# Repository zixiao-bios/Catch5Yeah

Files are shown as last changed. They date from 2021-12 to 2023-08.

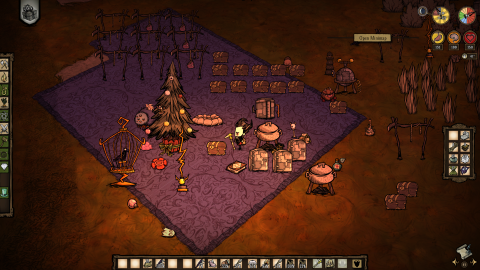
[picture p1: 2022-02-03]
ArtDesign/imgs/img_DST.png

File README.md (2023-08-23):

# Catch5Yeah

 A DIY claw machine as our 5th anniversary gift.

Assembly and operation video on bilibili: https://www.bilibili.com/video/BV1fP411p73M/

vlcsnap-2023-08-23-16h21m46s423

封面



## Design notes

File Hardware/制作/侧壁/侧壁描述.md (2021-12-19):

### 总览

+ 高度：650mm
+ 外径：400mm
+ 壁厚：5mm

共有 4 个特征：

+ 4 个顶部 L 形开槽
+ 1 个侧面圆角矩形开孔
+ 1 正面底部个方形开槽
+ 1 个背面底部胶囊形开孔

立体图如下：




俯视图相对位置：



下面一一说明每个特征的细节，下文中长度单位均为 mm，使用角度制。

### 4 个顶部 L 形开槽



+ 右图三个蓝色的平面都是**径向**的，不互相平行

### 1 个侧面圆角矩形开孔



+ 右图两个蓝色的平面是**平行**的

### 1 正面底部个方形开槽



+ 上图两个蓝色的平面是**径向**的，不平行

### 1 个背面底部胶囊形开孔



+ 上图两个蓝色平面是**平行**的

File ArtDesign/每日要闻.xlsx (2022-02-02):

配图 | 文字
饥荒小家 | 考古重大发现：x千万年历史洞穴发现史前壁画、火堆、烧焦的骨头等，将人类用火的历史提前，壁画内容改变人类对史前认知。网友指出壁画内容为知名生存游戏“饥荒”，游戏工作室科雷经过调查后发表声明称，该壁画系饥荒团队外出团建时，美工部门员工一时兴起所作，而火堆等痕迹系烧烤后的残留物。消息公布后国际社会对其破坏史前洞穴的行为一片谴责，受此负面消息影响，腾讯公司股价下跌超过10%，为今年最大单日跌幅。
坎巴拉合影 | NASA最新太空望远镜詹姆斯韦伯完成初期调试工作，向比邻星拍摄了第一张照片。竟然拍到了两个外星个体乘坐露天飞船远航的景象。照片一经爆出即掀起巨大舆论，主流舆论认为此为流浪太空的两个善良外星人，并在众筹网站发布名为“小绿人也是人，他们需要一个家！”的众筹项目。另有网友指出，该形象与知名航天沙盒游戏“Kerbal Space Programme”中十分相似，并据此推断该工作室早已与该文明建立秘密联系，并引导其攻占地球。但Xxx工作室公关部坚称该形象源自CEO儿子三岁时的美术作业。
美女亲嘴 | 新晋网红“露露奶黄包”，人民日报评论员文章："审丑"风气不可有

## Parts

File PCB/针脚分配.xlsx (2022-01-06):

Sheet: ESP32
GPIO | Intput | Output | Notes | 分配 | Function
0 | pulled up | OK | outputs PWM signal at boot Strapping pin | 74HC595D_SCK
1 | TX Pin | OK | debug output at boot | RGB2
2 | OK | OK | connected to on-board LED strapping pin | 74HC595D_RCK
3 | OK | RX Pin | HIGH at boot | K2
4 | OK | OK |  | TFT_MISO
5 | OK | OK | outputs PWM signal at boot strapping pin | TFT_MOSI
6 | NO | NO | 连接到集成 SPI Flash
7 | NO | NO | 连接到集成 SPI Flash
8 | NO | NO | 连接到集成 SPI Flash
9 | NO | NO | 连接到集成 SPI Flash
10 | NO | NO | 连接到集成 SPI Flash
11 | NO | NO | 连接到集成 SPI Flash
12 | OK | OK | boot fail if pulled high strapping pin | I2S_BLCK
13 | OK | OK |  | I2S_DIN
14 | OK | OK | outputs PWM signal at boot | I2S_LRC
15 | OK | OK | outputs PWM signal at boot strapping pin | 74HC595D_SI
16 | OK | OK |  | RTC_SCL
17 | OK | OK |  | TFT_SCLK
18 | OK | OK |  | TFT_DC
19 | OK | OK |  | RTC_SDA
21 | OK | OK |  | TFT_CS
22 | OK | OK |  | TOUCH_CS
23 | OK | OK |  | RGB1
25 | OK | OK |  | RGB3
26 | OK | OK |  | K1
27 | OK | OK |  | RGB4
32 | OK | OK |  | K3
33 | OK | OK |  | K4
34 | OK | NO | input only | S3
35 | OK | NO | input only | B1
36 | OK | NO | input only | S1
39 | OK | NO | input only | S2

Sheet: 74HC595D
Pin | 分配
Q0/QA
Q1/QB | MOTOR1
Q2/QC | MOTOR1
Q3/QD | MOTOR2
Q4/QE | MOTOR2
Q5/QF | MOTOR3
Q6/QG | MAG
Q7/QH | TFT_LED

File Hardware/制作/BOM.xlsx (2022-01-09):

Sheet: 紧固件
类别 | 型号 | 用途 | 数量 | 备注
弹簧垫圈 | M3 | 操纵台-屏幕-底板 | 4
垫圈 | M3*5*0.5 | 操纵台-屏幕-底板 | 4
弹簧垫圈 | M5 | 操纵台-摇杆-底板 | 4
平头螺丝 | M5*12 | 操纵台-摇杆-底板 | 4
平头螺丝 | M3*10 | 操纵台-屏幕-底板 | 4
防松螺母 | M5 | 操纵台-侧壁 | 2
平头螺丝 | M5*12 | 操纵台-侧壁 | 2
平头螺丝 | M5*12 | 操纵台-底板 | 4
弹簧垫圈 | M5 | 操纵台-底板 | 4
防松螺母 | M5 | 底板-侧壁 | 5
平头螺丝 | M5*12 | 底板-侧壁 | 5
薄螺母 | M4 | 底板-电机 | 4
弹簧垫圈 | M4 | 底板-电机 | 4
平头螺丝 | M4*10 | 底板-电机 | 4
防松螺母 | M5 | 顶盖-L锁 | 8
平头螺丝 | M5*35 | 顶盖-L锁 | 8
防松螺母 | M5 | 顶盖-皮带从动轮 | 2
平头螺丝 | M5*12 | 顶盖-皮带从动轮 | 2
防松螺母 | M5 | 顶盖-皮带主动轮 | 2
平头螺丝 | M5*18 | 顶盖-皮带主动轮 | 2
防松螺母 | M5 | 顶盖-顶盖密码锁 | 2
平头螺丝 | M5*12 | 顶盖-顶盖密码锁 | 2
防松螺母 | M5 | 侧壁-侧壁密码锁 | 2
平头螺丝 | M5*12 | 侧壁-侧壁密码锁 | 2
防松螺母 | M3 | 顶盖-滑块止动块 | 2
平头螺丝 | M3*20 | 顶盖-滑块止动块 | 2
平头螺丝 | M3*6 | 底板-开关电源 | 4
防松螺母 | M2.5 | 吊轮架-皮带扣 | 4
弹簧垫圈 | M2 | N20减速电机-皮带主动轮架 | 2
平头螺丝 | M2*8 | 顶盖密码锁-弹簧触点 | 1
平头螺丝 | M2*16 | 顶盖密码锁-弹簧触点 | 1
防松螺母 | M2 | 顶盖密码锁-弹簧触点 | 2
防松螺母 | M3 | 顶盖-灯条固定架 | 2
平头螺丝 | M3*10 | 顶盖-灯条固定架 | 2
防松螺母 | M3 | 红外接近开关 | 3
平头螺丝 | M3*10 | 红外接近开关 | 2
平头螺丝 | M3*10 | 红外接近开关 | 1
防松螺母 | M2.5 | 电磁铁架-导线扣 | 2
平头螺丝 | M2.5*8 | 电磁铁架-导线扣 | 2
平头螺丝 | M2.5*12 | 吊轮架-皮带扣 | 4
平头螺丝 | M4*10 | 吊轮架-滑块 | 4
弹簧垫圈 | M4 | 吊轮架-滑块 | 4
防松螺母 | M3 | 侧壁-出球口平台 | 4
平头螺丝 | M3*10 | 侧壁-出球口平台 | 4
热熔螺母 | M5*5*7 | 底板M5螺丝柱 | 8
热熔螺母 | M3*5*5 | 底板M3螺丝柱 | 4
热熔螺母 | M4*4*6 | 顶盖-滑轨 | 6
内六角螺丝 | M4*14 | 顶盖-滑轨 | 6
平头螺丝 | M3*10 | 转盘-传动法兰 | 4
防松螺母 | M3 | 转盘-传动法兰 | 4
平头螺丝 | M3*10 | 挡板-转盘 | 12
防松螺母 | M3 | 挡板-转盘 | 12
防松螺母 | M2 | RGB灯条卡槽-侧壁 | 16
平头螺丝 | M2*10 | RGB灯条卡槽-侧壁 | 16
平头螺丝 | M2*8 | 侧壁密码锁-弹簧触点 | 2
防松螺母 | M2 | 顶盖密码锁-弹簧触点 | 2
垫圈 | M4*7*1 | 吊轮架-滑块 | 4
平头螺丝 | M3*20 | 侧壁-AC电源插座 | 2
防松螺母 | M3 | 侧壁-AC电源插座 | 2
防松螺母 | M3 | 底板-PCB | 4
平头螺丝 | M3*10 | 底板-PCB | 4
垫圈 | M3*5*0.5 | 底板-PCB | 8
弹簧垫圈 | M3 | 底板-PCB | 4
平头螺丝 | M6*16 | 顶盖-提手 | 2
弹簧垫圈 | M6 | 顶盖-提手 | 2
垫圈 | M6*20*1 | 顶盖-提手 | 2

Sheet: 铁盒
名称 | 形状 | 内容 | 尺寸/mm | 数量
小猪佩奇集趣球 | 球形 | 奶片 | 70 | 12
0号球 | 球形 | 纪念 | 70 | 1
小方盒 | 方形 | 首饰 | 75*75*65
大方盒 | 方形 |  | 94*94*90
扁圆盒 | 包子 | 口红 | 90*90*65

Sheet: Sheet1
皮带扣 | 螺母位过大
线轮 | 凹槽过浅
吊轮架 | 降低皮带扣位置，以防止皮带空转
操作台 | 边缘突出底盘侧壁，中部低于侧壁开槽
RGB灯条卡槽 | 螺母位过大
L锁 | 突出部分位置过高
顶盖密码锁 | 去除弹簧触点支架
侧壁密码锁 | 密码锁开孔过小；去除弹簧触点支架

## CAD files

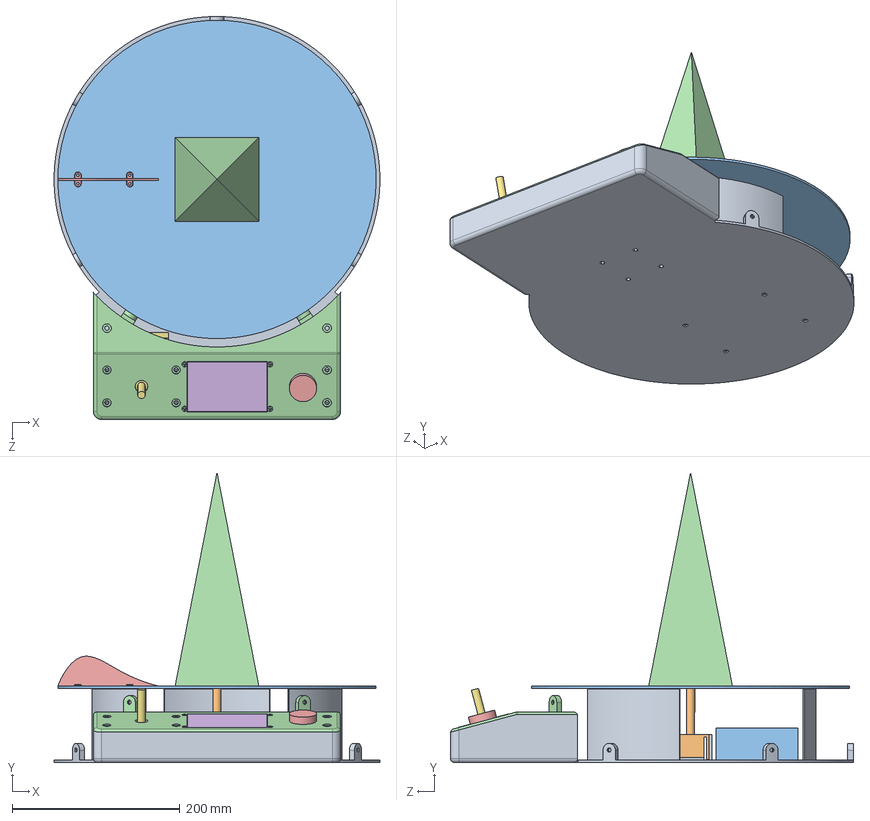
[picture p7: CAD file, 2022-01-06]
Hardware/底座/底座.SLDASM
389.0 x 346.4 x 481.1 mm
底盘
底盘电机
开关电源
操纵台顶盖
按钮
显示屏2
摇杆
M3弹簧垫圈 x 4
垫圈M3x5x0.5 x 4
M5弹簧垫圈 x 8

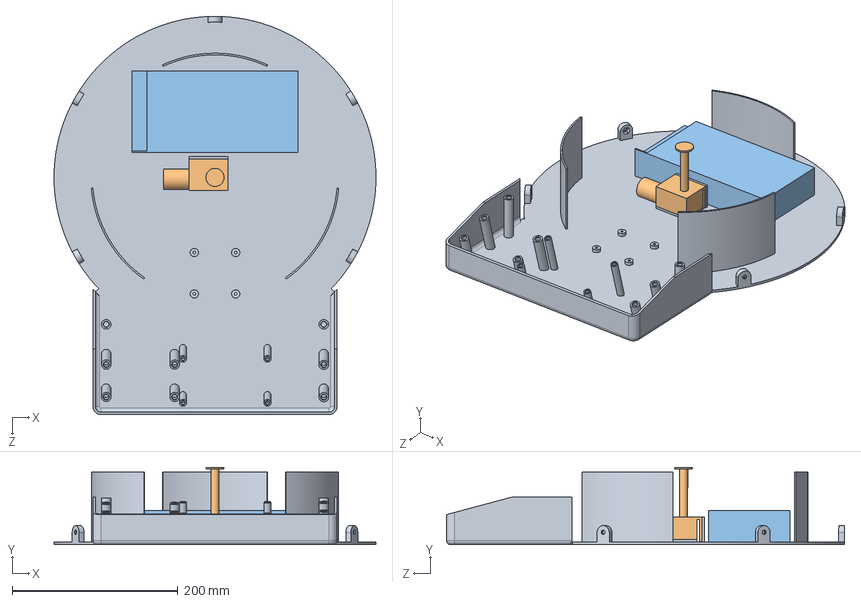
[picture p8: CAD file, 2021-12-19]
Hardware/底座/底盘/底盘.SLDASM
389.0 x 93.4 x 481.1 mm
底盘
底盘电机
开关电源

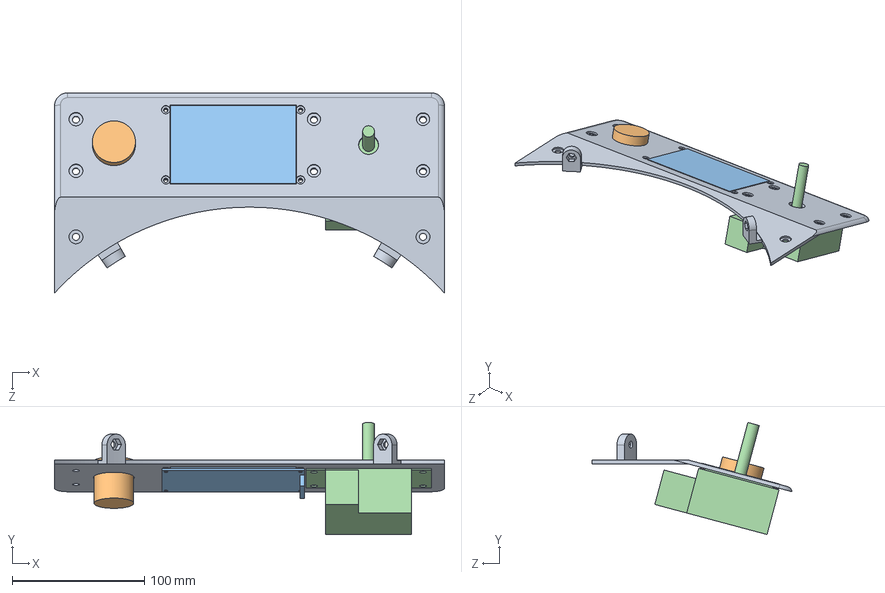
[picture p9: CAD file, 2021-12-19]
Hardware/底座/操纵台/操纵台.SLDASM
295.3 x 84.9 x 151.7 mm
操纵台顶盖
按钮
显示屏2
摇杆
M3弹簧垫圈 x 4
垫圈M3x5x0.5 x 4

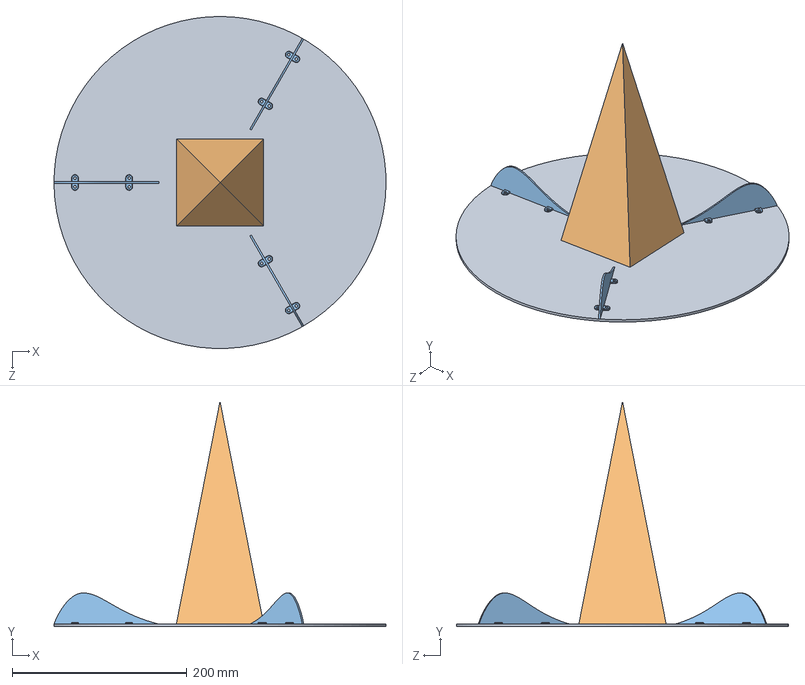
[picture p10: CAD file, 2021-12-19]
Hardware/底座/转盘/转盘.SLDASM
380.0 x 258.0 x 380.0 mm
转盘
塔
挡板 x 3

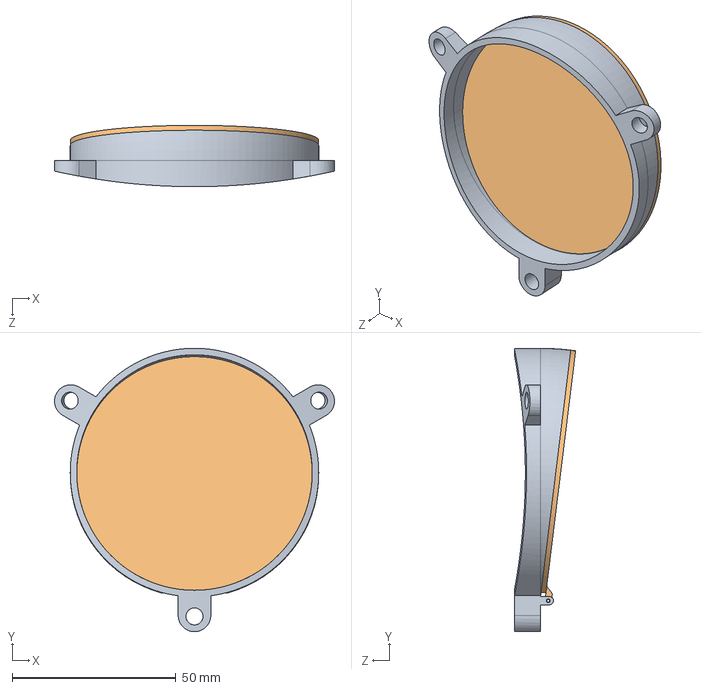
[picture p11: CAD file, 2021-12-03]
Hardware/投放口/投放口.SLDASM
85.6 x 86.7 x 18.8 mm
投放口 拼接
投放口盖子

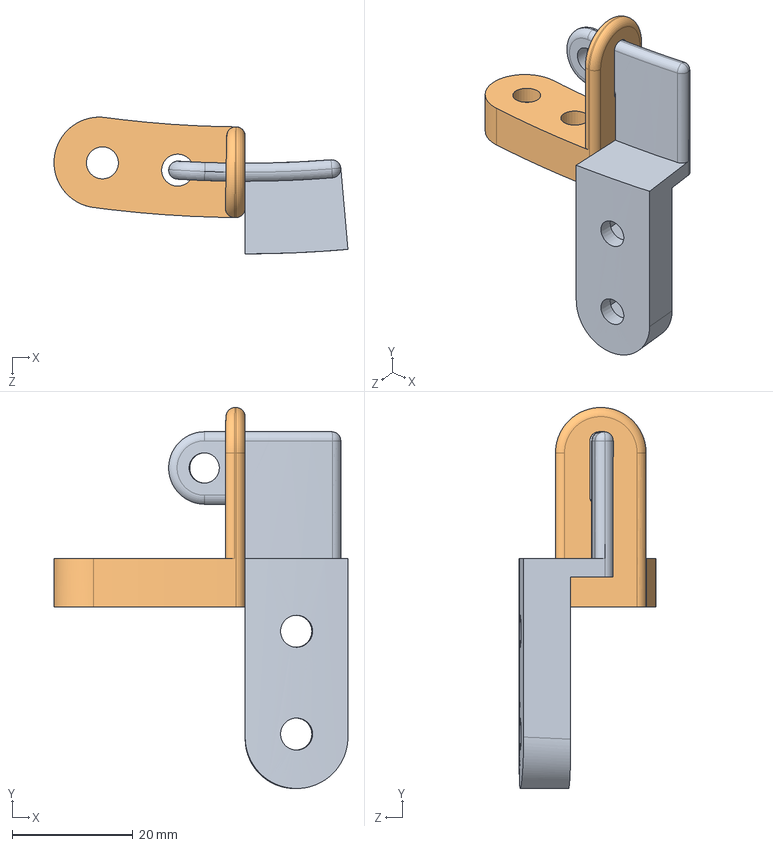
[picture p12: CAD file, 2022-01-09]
Hardware/顶盖-侧壁连接器/顶盖-侧壁连接器.SLDASM
48.6 x 63.0 x 22.6 mm
侧壁密码锁
顶盖密码锁

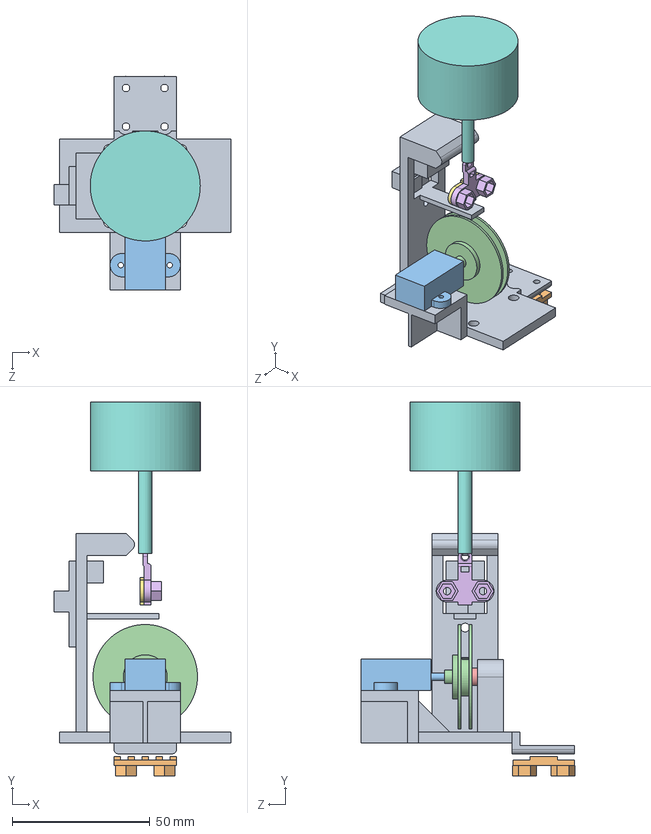
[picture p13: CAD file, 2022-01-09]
Hardware/顶盖/吊轮/吊轮.SLDASM
64.3 x 136.0 x 77.7 mm
吊轮架
皮带扣
N20减速电机
线轮
导电滑环-紧凑
电磁铁架
导线扣
电磁铁
红外接近开关

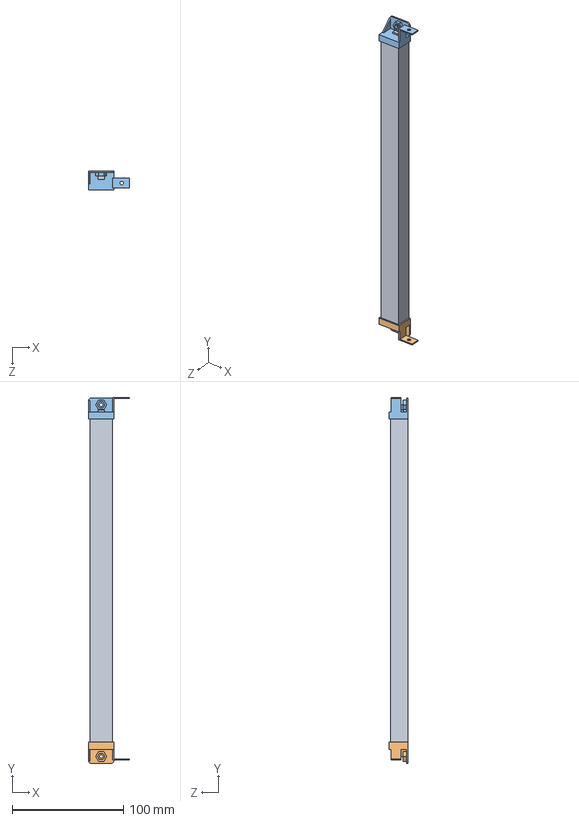
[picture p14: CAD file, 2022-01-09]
Hardware/顶盖/灯条/灯条.SLDASM
37.0 x 328.5 x 17.0 mm
灯条
灯条固定架1
灯条固定架2

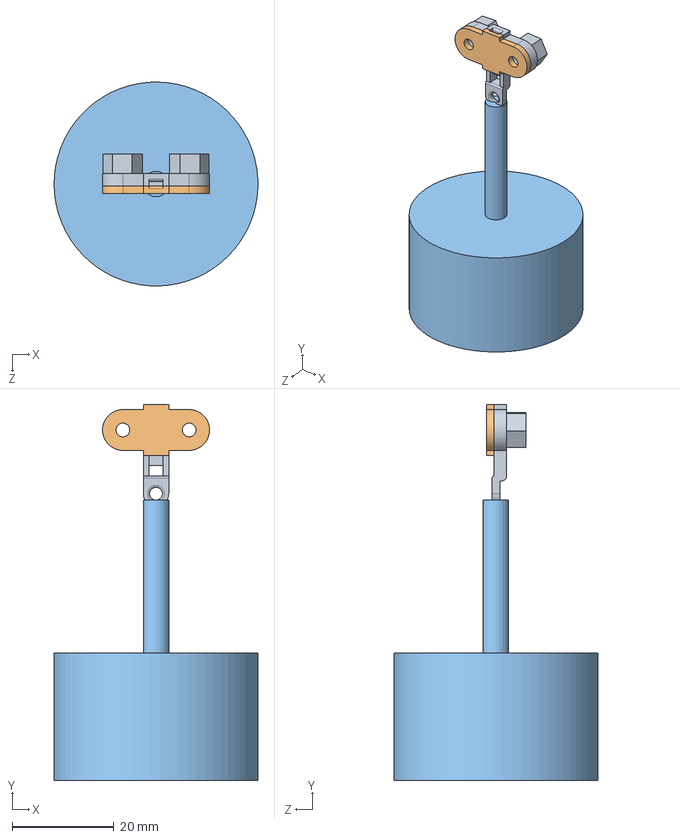
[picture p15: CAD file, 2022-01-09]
Hardware/顶盖/电磁铁架/电磁铁架.SLDASM
40.0 x 73.8 x 40.0 mm
电磁铁架
导线扣
电磁铁

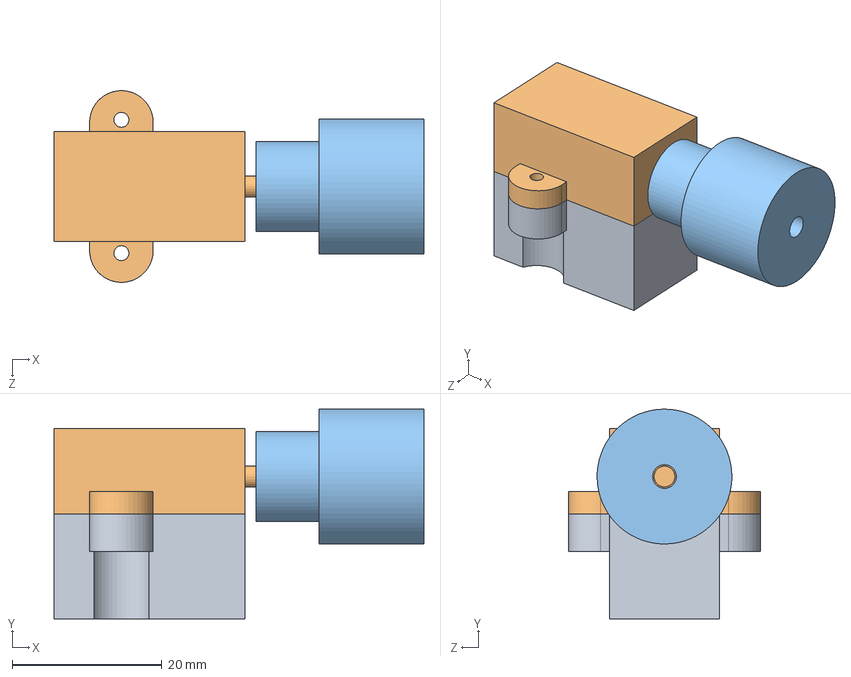
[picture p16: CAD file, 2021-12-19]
Hardware/顶盖/皮带主动轮/皮带主动轮.SLDASM
49.4 x 28.0 x 25.6 mm
皮带主动轮架
N20减速电机
皮带轮

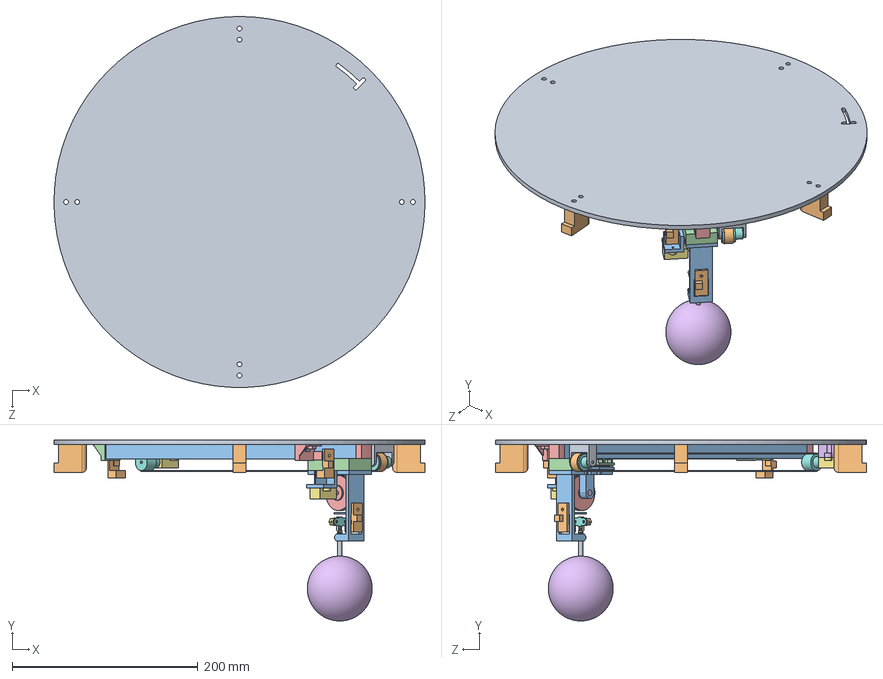
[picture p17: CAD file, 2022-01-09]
Hardware/顶盖/顶盖.SLDASM
400.0 x 195.1 x 400.0 mm
顶盖
顶盖L锁 x 4
滑轨
滑块
滑块止动块 x 2
皮带主动轮架
N20减速电机 x 2
皮带轮 x 2
皮带从动轮架
皮带1-3^顶盖
吊轮架
皮带扣
线轮
导电滑环-紧凑
电磁铁架
导线扣
电磁铁
红外接近开关 x 3
灯条
灯条固定架1
灯条固定架2

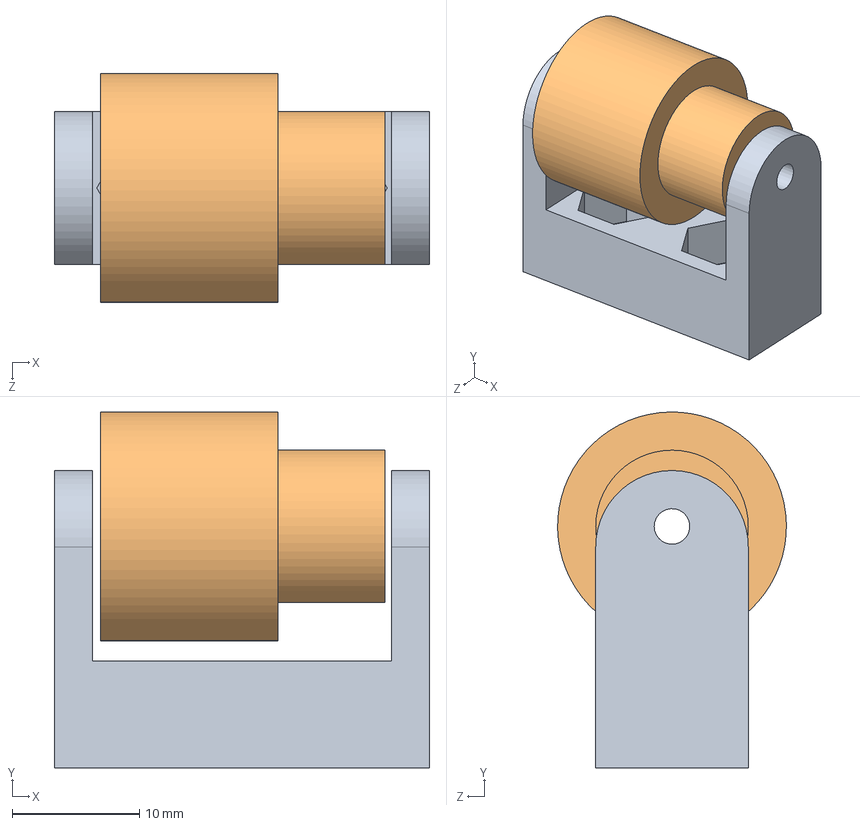
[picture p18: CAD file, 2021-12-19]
Hardware/顶盖/皮带从动轮/皮带从动轮.SLDASM
29.5 x 28.0 x 18.0 mm
皮带从动轮架
皮带轮

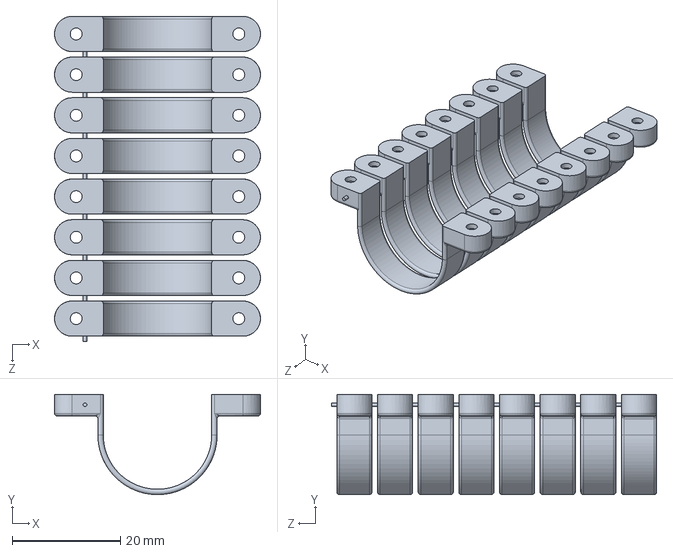
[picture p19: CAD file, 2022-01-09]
Hardware/part/RGB灯条卡槽 - 8合1.SLDPRT
38.0 x 18.5 x 60.0 mm

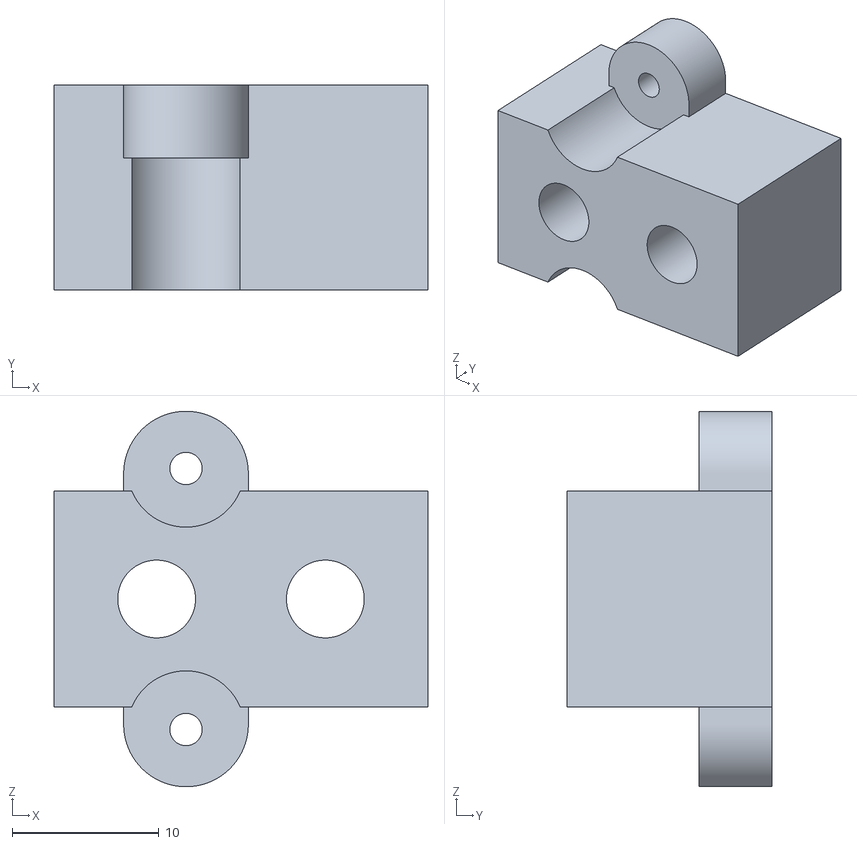
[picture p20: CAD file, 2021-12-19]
Hardware/制作/3D打印/01/皮带主动轮架.STL
25.5 x 14.0 x 25.6

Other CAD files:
Hardware/制作/3D打印/02/顶盖L锁-修正1.STL
Hardware/制作/3D打印/03/线轮.STL
Hardware/制作/侧壁/侧壁.STEP
Hardware/制作/顶盖、转盘/顶盖图纸.DXF
Hardware/part/M3弹簧垫圈.SLDPRT
Hardware/part/M5弹簧垫圈.SLDPRT
Hardware/part/RGB灯带 圆形.SLDPRT
Hardware/part/RGB灯条卡槽.SLDPRT
Hardware/part/侧壁.SLDPRT
Hardware/part/垫圈M3x5x0.5.SLDPRT
Hardware/part/大铁盒.SLDPRT
Hardware/part/小铁盒.SLDPRT
Hardware/part/红外接近开关.SLDPRT
Hardware/part/铁球.SLDPRT
Hardware/制作/3D打印/01/吊轮架.STL
Hardware/制作/3D打印/01/导线扣.STL
Hardware/制作/3D打印/01/操纵台顶盖.STL
Hardware/制作/3D打印/01/滑块止动块.STL
Hardware/制作/3D打印/01/灯条固定架1.STL
Hardware/制作/3D打印/01/灯条固定架2.STL
Hardware/制作/3D打印/01/皮带从动轮架.STL
Hardware/制作/3D打印/01/皮带扣.STL
Hardware/制作/3D打印/01/线轮.STL
Hardware/制作/3D打印/01/顶盖L锁.STL
Hardware/制作/3D打印/02/顶盖L锁-修正2.STL
Hardware/制作/3D打印/02/顶盖L锁-修正3.STL
Hardware/制作/3D打印/02/顶盖L锁-修正4.STL
Hardware/制作/3D打印/03/侧壁密码锁.STL
Hardware/制作/3D打印/03/吊轮架.STL
Hardware/制作/3D打印/03/皮带扣.STL
Hardware/制作/3D打印/03/顶盖L锁-修正1.STL
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

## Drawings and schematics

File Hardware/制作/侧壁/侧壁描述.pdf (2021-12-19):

总览

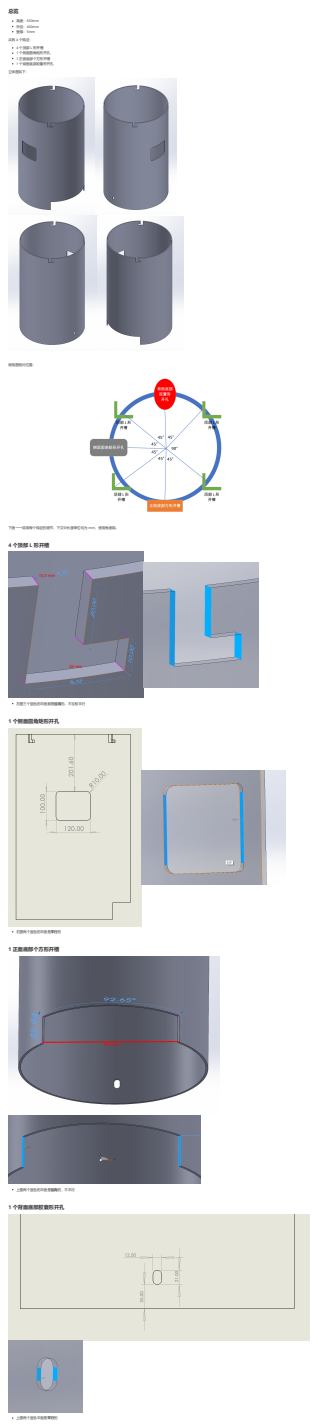
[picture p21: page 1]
共有 4 个特征：; 4 个顶部 L 形开槽 1 个侧面圆角矩形开孔 1 正面底部个方形开槽 1 个背面底部胶囊形开孔; 立体图如下：; 俯视图相对位置：; 4 个顶部 L 形开槽; 右图三个蓝色的平面都是径向的，不互相平行; 1 个侧面圆角矩形开孔; 右图两个蓝色的平面是平行的; 1 正面底部个方形开槽; 上图两个蓝色的平面是径向的，不平行; 1 个背面底部胶囊形开孔; 上图两个蓝色平面是平行的

下面一一说明每个特征的细节，下文中长度单位均为 mm，使用角度制。

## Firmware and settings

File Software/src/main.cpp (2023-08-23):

#include <Arduino.h>
#include <freertos/FreeRTOS.h>
#include <LITTLEFS.h>

#include "Display.h"
#include "RGB_Strip.h"
#include "Network.h"
#include "Claw.h"
#include "Setup.h"
#include "RTC.h"
#include "Tool.h"
#include "music.h"

RGB_Strip *rgb1, *rgb2, *rgb3, *rgb4;

[[noreturn]] void displayTask(void *pv) {
    while (true) {
        delay(5);
        xSemaphoreTake(lvgl_mutex, portMAX_DELAY);
        lv_task_handler();
        xSemaphoreGive(lvgl_mutex);
    }
}

__attribute__((unused)) void setup() {
    Serial.begin(115200);
    Serial.println("\n===============start===============");

    // start LittleFS
    if (!LITTLEFS.begin(true)) {
        Serial.println("LittleFS Mount Failed!");
    }

    rtc_init();

    // read setup file
    init_setup();

    // init music player
    music_init();

    // init claw
    claw_init();
    claw_reset_async();

    // init display
    displayInit();
    show_screen("main");
    xTaskCreatePinnedToCore(displayTask, "DisplayTask", 10000, nullptr, 1, nullptr, 1);

    // init WiFi
    if (setup_doc["wifi"]["enable"]) {
        xTaskCreatePinnedToCore(UI_turn_on_wifi_task, "TurnOnWifi", 10000, nullptr, 1, nullptr, 0);
    }

    // init RGB
    rgb1 = new RGB_Strip(1);
    rgb1->setEffect(RGB_RAINBOW);

//    rgb2 = new RGB_Strip(2);
//    rgb2->setEffect(RGB_OFF);

    rgb3 = new RGB_Strip(3);
    rgb3->setEffect(RGB_RAINBOW);

    rgb4 = new RGB_Strip(4);
    rgb4->setEffect(RGB_RAINBOW);
}

__attribute__((unused)) void loop() {}

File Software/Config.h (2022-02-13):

#ifndef SOFTWARE_CONFIG_H
#define SOFTWARE_CONFIG_H

/**======================
 * 1. ESP32 pin settings
 **======================*/

// Display pin defined in ./platformio.ini

// I2S pin
#define PIN_I2S_LRC 14
#define PIN_I2S_BLCK 12
#define PIN_I2S_DIN 13

// RTC pin
#define PIN_RTC_SDA 19
#define PIN_RTC_SCL 16

// RGB pin
#define PIN_RGB1 23
#define PIN_RGB2 1
#define PIN_RGB3 25
#define PIN_RGB4 27

// keypad, button
#define PIN_KEY_DOWN 26
#define PIN_KEY_UP 3
#define PIN_KEY_RIGHT 32
#define PIN_KEY_LEFT 33
#define PIN_BTN 35

// shift register
#define PIN_SR_SCK 0
#define PIN_SR_RCK 2
#define PIN_SR_SI 15

// motor, electromagnet
#define SR_PIN_M1A 1
#define SR_PIN_M1B 2
#define SR_PIN_M2A 3
#define SR_PIN_M2B 4
#define SR_PIN_M3 5
#define SR_PIN_MAG 6

// proximity switch
#define PIN_S_RIGHT 36
#define PIN_S_LEFT 39
#define PIN_S_UP 34

// screen backlight
#define SR_PIN_SCREEN 7


/**======================
 * 2. Display & Touch screen
 **======================*/
#define DISPLAY_WIDTH 320
#define DISPLAY_HEIGHT 480
#define SCREEN_WIDTH DISPLAY_HEIGHT
#define SCREEN_HEIGHT DISPLAY_WIDTH
#define SCREEN_ROTATION 3
#define CALIBRATION_FILE "/TouchCalData"

// colors
#define COLOR_GOOD 0x00cc00
#define COLOR_NORMAL 0xFF7800
#define COLOR_BAD 0xff0000


/**======================
 * 3. RGB Strip
 **======================*/
// settings
#define STRIP_NUM 3
#define RGB_BRIGHTNESS 128
#define RGB1_NUM_LEDS 111
#define RGB2_NUM_LEDS 111
#define RGB3_NUM_LEDS 113
#define RGB4_NUM_LEDS 41

// RGB effect definition
# define RGB_OFF 0
# define RGB_RAINBOW 1
# define RGB_THEATER_RAINBOW 2


/**======================
 * 4. Datetime
 **======================*/
#define DATETIME_BEGIN_YEAR 2016
#define DATETIME_BEGIN_MONTH 12
#define DATETIME_BEGIN_DAY 25
#define DATETIME_BEGIN_HOUR 21
#define DATETIME_BEGIN_MIN 50

#endif //SOFTWARE_CONFIG_H

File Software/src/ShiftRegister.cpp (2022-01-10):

#include <Arduino.h>
#include <SPIFFS.h>
#include <FastLED.h>

#include "Audio.h"

// unused
#include <TFT_eSPI.h>

#include "FS.h"
#include <SPI.h>
#include <TFT_eSPI.h>
#include "FS.h"
#include <SPI.h>
#include <TFT_eSPI.h>

#include <ShiftRegister74HC595.h>

ShiftRegister74HC595<1> sr(15, 0, 2); // NOLINT

void setup() {
    Serial.begin(115200);
    pinMode(35, INPUT);
}

void loop() {
    Serial.println(digitalRead(35));
    delay(50);
//    sr.setNoUpdate(1, HIGH);
//    sr.setNoUpdate(2, LOW);
//    sr.updateRegisters();
//    delay(2000);
//
//    sr.setNoUpdate(1, LOW);
//    sr.setNoUpdate(2, HIGH);
//    sr.updateRegisters();
//    delay(2000);
}

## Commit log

2021-12-03 add sw model files
    [N20减速电机.SLDPRT, 侧壁.SLDPRT, 侧壁锁支架.SLDPRT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]
2021-12-09 finish console hardware model
    [BOM.xlsx, M3弹簧垫圈.SLDPRT, M5弹簧垫圈.SLDPRT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]
2021-12-15 add LED lib and demo
2021-12-19 finish sw model
    [BOM.xlsx, N20减速电机.SLDPRT, RGB灯带 圆形.SLDPRT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]
2022-01-06 finish hardware second stage
    [BOM.xlsx, 吊轮.SLDASM, 吊轮架.SLDPRT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]
2022-01-09 finish hardware third stage
    [BOM.xlsx, RGB灯条卡槽 - 8合1.SLDPRT, RGB灯条卡槽.SLDPRT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]
2022-01-16 add touch calibrate function
2022-01-19 add pin config of keypad and button
2022-01-27 update partition table and platformIO configuration
    [partition.csv]
2022-02-02 add buttons in main page
2022-02-02 update lvgl version to 8.2.0, change to manual import in lib/
    [每日要闻.xlsx, 设计元素.xlsx]
2022-02-03 very, very strange bug...
    已发现的复现必要条件：font_small.h字符集合，Display.cpp settingScreenLoad()函数中label字符顺序。
    bug描述：在特定label中使用font_small字体显示“其它”时出现空指针错误，而显示“其”、“它”、“其 它”均无错误。且向该字体追加其它字模后，问题消失。
    使用的字模软件：MCU_Font V2.0 (https://gitee.com/WuBinCPP/MCU_Font_Release)
    [main.cpp]
2022-02-03 add callback for buttons
2022-02-04 pin lv_tasks to same CPU core
2022-02-04 move some storage space from spiffs to app0
    [partition.csv]
2022-02-04 move all lvgl task to one thread
2022-02-04 so... f**k you thread safety!
2022-02-05 add wifi connect button and limit length of wifi list
2022-02-05 fix show and hidden of wifi widgets, fix color config
    [Config.h, main.cpp]
2022-02-05 send wifi_name and password when click connect button
2022-02-06 fix turn on/off wifi
    [Network.cpp, main.cpp]
2022-02-07 pin RGB thread to core 1
2022-02-07 add motor pins
2022-02-07 fix motor pins
2022-02-07 rename key pin
2022-02-07 add claw control
2022-02-07 rename switch pin
2022-02-07 stop move when claw reach the end
2022-02-07 fix claw move logic
    [Claw.cpp]
2022-02-07 fix claw control logic
    [Claw.cpp]
2022-02-08 add stay_top function, fix logic
    [Claw.cpp, main.cpp]
2022-02-10 disable watchdog in ClawGrab task
2022-02-10 push button second time
2022-02-10 add grab back button cb
2022-02-10 add grab start and finish button cb
2022-02-14 pin audio task to core0, and increase core0 claw tasks' priority
2022-02-15 pin audio task to core1
2022-02-15 fix thread safety problem of RTC
    [RTC.cpp]
2022-02-15 fix RTC mutex bug
    [RTC.cpp]
2023-08-23 add PCB file
    [1_P1.schdoc, 1_Part_MCU.schdoc, 2_Part_Conveter.schdoc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]
